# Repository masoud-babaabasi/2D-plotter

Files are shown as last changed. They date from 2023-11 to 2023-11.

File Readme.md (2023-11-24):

# 2D plotter(Using Pen)
### My bachelor's degree final project
This project is inspired by a device called [AxiDraw](https://www.axidraw.com/). This device holds a pen and then draws like anything that is programmed on it, like a human being. I decided to replicate this device functionality and build a device for myself and decided to present it as my bachelor's degree project.

## Mechanical Structure
This project relies on a mechanical structure called T-bot.

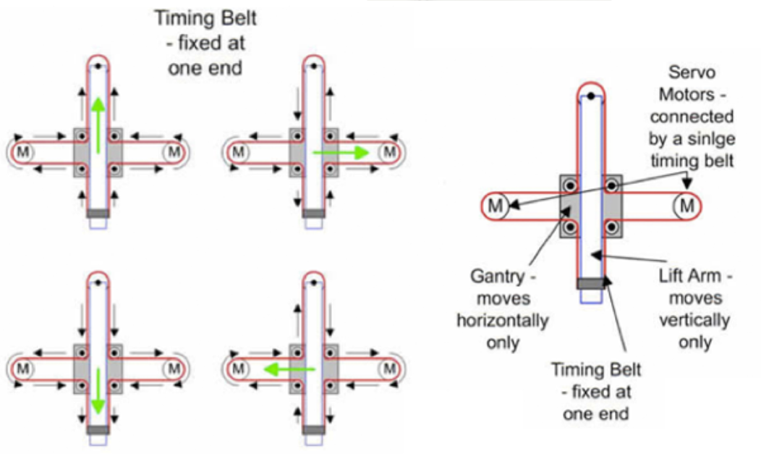
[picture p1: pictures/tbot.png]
t-bot structure

I made the mechanical structure using some CNC machine parts like timing belt, pulleys, rails, and wagons. The advantages of using a T-bot structure is that the motors are fixed and mounted on the chasie and it only needs one timing belt. In this picture two stepper motors are mounted on the sides of one of the rails. The second rail is moving alongside the first one.

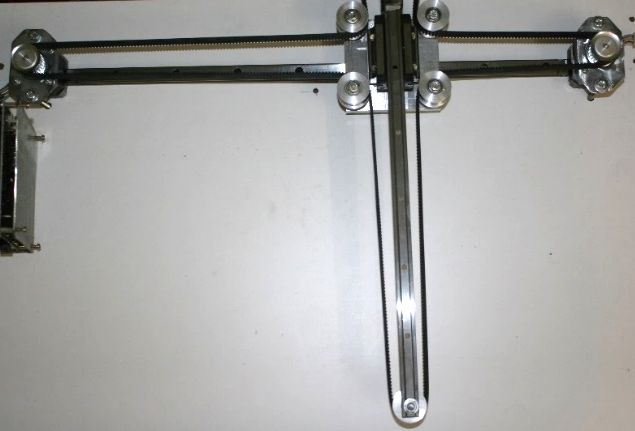
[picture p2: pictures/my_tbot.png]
my t-bot

## Electronic Hardware
I designed the board for the project using Altium Designer. The board is powered by an Atmega2560. There are two L298 power amplifiers for driving each stepper motor. A 2 by 16 character LCD displays the messages and a 4 by 4 keypad alongside a joystick are utilized to receive input from the user. A little servo motor is mounted on the pen holder which can lift the pen up whenever needed. The board supply is 12 volts and there are 3 switching LM2596 that provide adequate voltages for motors and electronics circuit.
board
## Software
The code for the project is written in [Arduino](https://www.arduino.cc/). I also wrote a custom library for controlling the T-bot structure in C++.
For testing there I draw some geometric shapes like spirals. These spirals are drawn via calculation of some polar equations. 
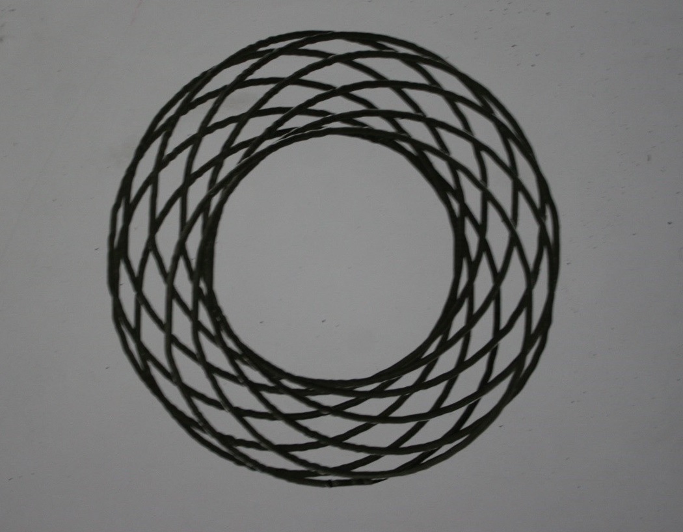
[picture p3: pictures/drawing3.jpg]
spiral

For drawing random shapes like humans, first, we need to draw or insert the shape in one of the CNC machine software. The software then outputs in a format called G-code. Conventional CNC machines can interpret this G-code and do the moves. But my Arduino code can not read G-code and only accepts inputs in the form of XY coordinates. So I wrote a Matlab script that reads the G-code file and outputs the XY sequence. 

In the pictures below, you can see my name being written. The drawing is converted from a G-code that I extracted.
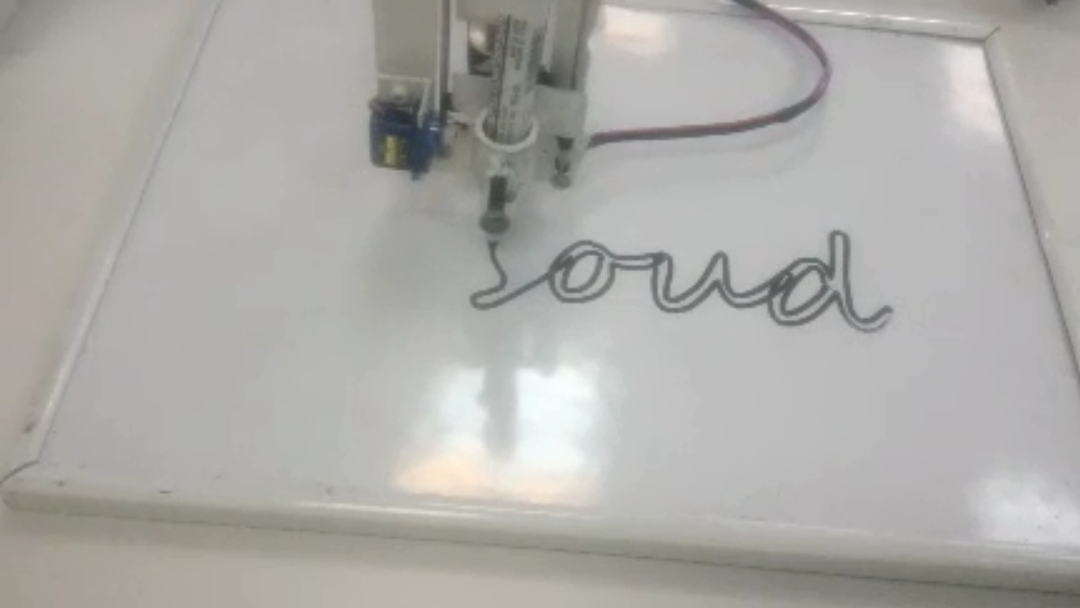
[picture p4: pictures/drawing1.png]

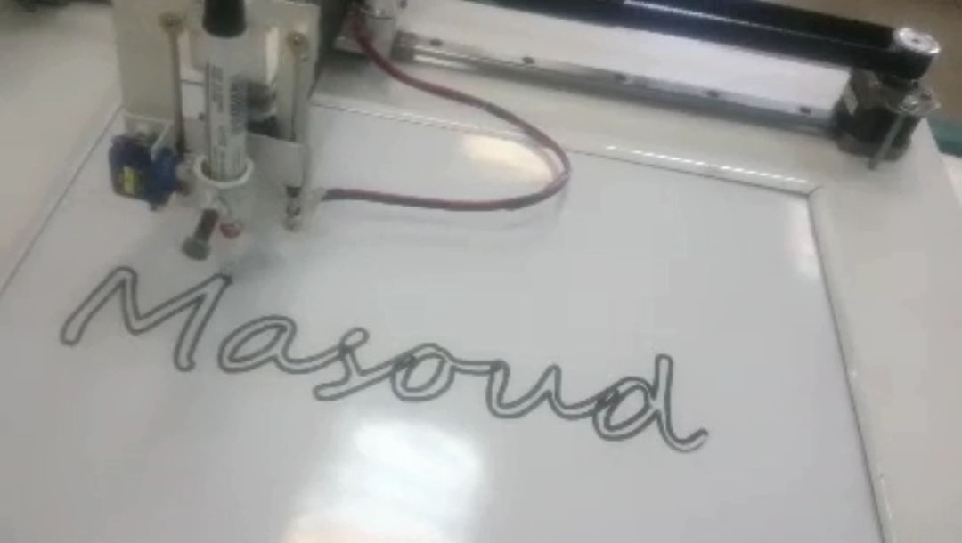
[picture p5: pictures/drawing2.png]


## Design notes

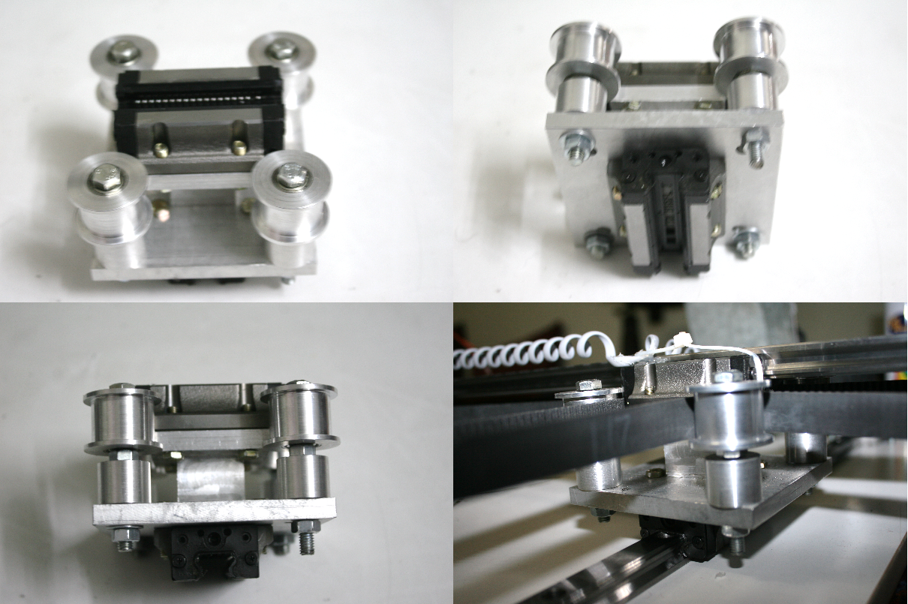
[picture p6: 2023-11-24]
pictures/wagon.png

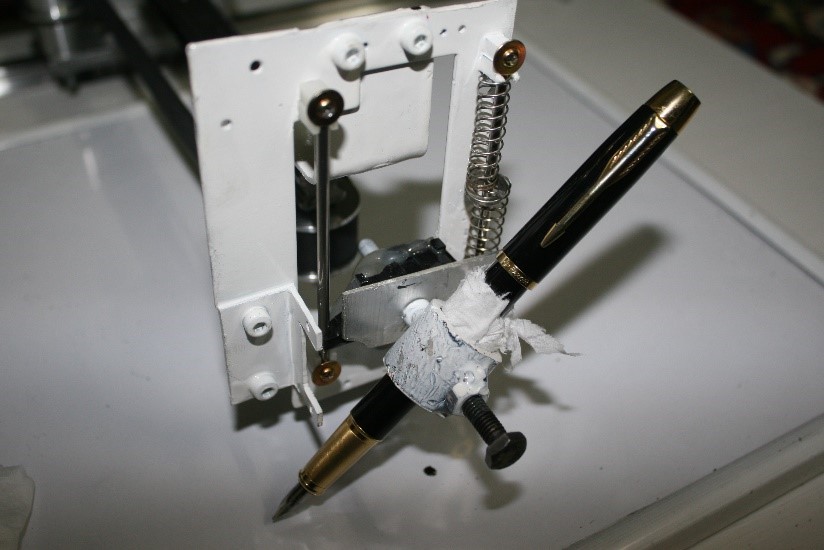
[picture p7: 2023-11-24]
pictures/pen_holder.jpg

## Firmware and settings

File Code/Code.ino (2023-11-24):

#include <Servo.h>
#include <Keypad.h>
#include <LiquidCrystal.h>
#include <Stepper.h>
#include <SPI.h>
#include <SD.h>
/* 
 *  Author: Masoud Babaabasi 
 *  Email: masoud.tafresh@gmail.com
 *  Version 1 created 28/8/2017
 *  For the perpose of this project the origanal library of Arduino PINS "pins_arduino.h" 
 *  for mega2560 is changed 
 *  "C:\Program Files\arduino-1.8.3\hardware\arduino\avr\variants\mega\pins_arduino.h"
 *  The changes are{
 *                            changing PG5 to PH2 for digital pin NO4 //lines 169 and 244
 *                            changing PG2 to PE6 for digital pin NO 39 // line 204 and 279
 *                            changing PG1 to PE2 for digital pin NO 40//line 205 and 
 *                            }
  */
/************************************************************************************************************************************/
/************************************************************************************************************************************/
/*
 * pin assignment
 */
#define SERVO_PIN 11
#define LCD_BACK A14
#define BUZ A15

#define Y_AX A0
#define X_AX A1
#define JOY_SW A3

#define ST1_1 43
#define ST1_2 42
#define ST1_3 45
#define ST1_4 44
#define ST1_E 46

#define ST2_1 3
#define ST2_2 39
#define ST2_3 5
#define ST2_4 2
#define ST2_E 40
#define stepsPerRevolution 200

#define MS1 25  // Micro switch NO1
#define MS2 26  // Micro switch NO2
#define MS3 27  // Micro switch NO3
#define MS4 28  // Micro switch NO4

#define chipSelect 10 // chip select of SD card

#define Rd 13  //reduis of the pully
#define UP 180
#define DOWN 90

#define LCD_ON digitalWrite(LCD_BACK,HIGH)
#define LCD_OFF digitalWrite(LCD_BACK,LOW)
#define BUZ_ON digitalWrite(BUZ,HIGH)
#define BUZ_OFF digitalWrite(BUZ,LOW)
#define ST1_EN digitalWrite(ST1_E,HIGH)
#define ST2_EN digitalWrite(ST2_E,HIGH)
#define ST1_DIS digitalWrite(ST1_E,LOW)
#define ST2_DIS digitalWrite(ST2_E,LOW)
#define HomeX -200
#define HomeY -130
#define xMax 200
#define xMin -200
#define yMax 130
#define yMin -130
/************************************************************************************************************************************/
/************************************************************************************************************************************/
LiquidCrystal lcd(A8, A9, A10, A11, A12, A13);
/************************************************************************************************************************************/
/************************************************************************************************************************************/
const byte ROWS = 3; //three rows
const byte COLS = 3; //three columns
char keys[ROWS][COLS] = {
  {'1','2','3'},
  {'4','5','6'},
  {'7','8','9'},
};
byte rowPins[ROWS] = {7,8,9}; //connect to the row pinouts of the keypad
byte colPins[COLS] = {4, 6,53}; //connect to the column pinouts of the keypad

Keypad keypad = Keypad( makeKeymap(keys), rowPins, colPins, ROWS, COLS );
/************************************************************************************************************************************/
/************************************************************************************************************************************/
Servo pen;
Stepper stepper1(stepsPerRevolution, ST1_1, ST1_2, ST1_3, ST1_4);
Stepper stepper2(stepsPerRevolution, ST2_1, ST2_2, ST2_3, ST2_4);
/************************************************************************************************************************************/
/************************************************************************************************************************************/
float preX,preY,preZ;
int sp = 120;
File shape,back;
/************************************************************************************************************************************/
/************************************************************************************************************************************/
void gotoXY(float inX,float inY);
void goHome();
void drawSnail(float centerX, float centerY);
void drawRose(float centerX, float centerY, float R);
void manualDraw();
void drawStar(float centerX, float centerY, float R);
void drawFiveangle(float centerX, float centerY, float A);
void drawStar2(float centerX, float centerY, float R);
void drawCircle(float centerX, float centerY, float R);
void spirograph(float r,float R,float w,bool sign);
void spirograph2();
/************************************************************************************************************************************/
/************************************************************************************************************************************/
void setup() {
 pen.attach(SERVO_PIN); 
 pen.write(UP);
 Serial.begin(115200);
 lcd.begin(16, 2);
pinMode(LCD_BACK,OUTPUT);
pinMode(BUZ,OUTPUT);
pinMode(ST2_E,OUTPUT);
pinMode(ST2_E,OUTPUT);
ST1_EN;
ST2_EN;
preX = HomeX;
preY = HomeY;
preZ = 1;
lcd.print("setup OK!");
LCD_ON;
delay(600);
lcd.clear();
/**********************************/
/**********************************/
stepper1.setSpeed(sp);
stepper2.setSpeed(sp);
//drawSnail(0,0);
//drawRose(0,0,80);
//drawStar(0,0,80);
//drawFiveangle(0,0,94);
//drawStar2(0,0,80);
//spirograph(70,20,10,0);
//spirograph2();
//drawCircle(0,0,100);
/*for(int i=5;i<=80;i+=15) {
  drawCircle(0,0,i);
  delay(600);
}*/
/*for(int i=5;i<=85;i+=10) {
  drawRose(0,0,i);
  delay(600);
}*/
  //draw Square
  /*gotoXY(80,80);
  gotoXY(80,-80);
  gotoXY(-80,-80);
  gotoXY(-80,80);
  gotoXY(80,80);*/
  //SD card read formated data
   /*if (!SD.begin(chipSelect)) lcd.print(F("Card failed, or not present"));
   shape = SD.open("masoud.txt", FILE_READ);
   back = SD.open("backup.txt",FILE_WRITE);
   shape.setTimeout(1);
   if(shape){
    String str,stX,stY;
    float x,y;
    while(shape.position() != shape.size()){
    str =shape.readStringUntil(',');
    if( str.startsWith(F("x=-")))  {
      stX = str.substring(3);
      x = stX.toFloat();
      x= -x;
    }
   else if( str.startsWith(F("x=")))  {
      stX = str.substring(2);
      x = stX.toFloat();
    }
      str =shape.readStringUntil('\n');
    if( str.startsWith(F("y=-")))  {
      stY = str.substring(3);
      y = stY.toFloat();
      y= -y;
    }
   else if( str.startsWith(F("y=")))  {
      stY = str.substring(2);
      y = stY.toFloat();
    }
    gotoXY(x,y);
    //back.print("x=");
    //back.print(x);
    //back.print(",y=");
   // back.println(y);
   // for(int i=0;i<5;i++) str =shape.readStringUntil('\n');
    }

   }
   shape.close();
   back.close();
   lcd.print("done");*/
   
}
void loop() {
  int i;
  String rec,stX,stY,stZ,str;
  float x,y,z;
 char key = keypad.getKey();
 if(key){
  lcd.clear();
  lcd.print(key);
  switch(key){
    case '1': lcd.print("Draw a star");
                  drawStar2(0,0,80);
                  lcd.clear();
                  break;
   case '2': lcd.print("Draw a pentagonangle");
                  drawFiveangle(0,0,94);
                  lcd.clear();
                  break;
   case '3': lcd.print("Draw a Rose");
                  drawRose(0,0,80);
                  lcd.clear();
                  break;
   case '4': lcd.print("Draw a Spirograph");
                  spirograph(70,20,10,0);
                  lcd.clear();
                  break;
   case '5': lcd.print("Draw a Spirograph");
                  spirograph2();
                  lcd.clear();
                  break;
   case '6': lcd.print("Draw a Snail");
                  drawSnail(0,0);
                  lcd.clear();
                  break;
   case '7': lcd.print("Draw masoud");
                    if (!SD.begin(chipSelect)) lcd.print(F("Card failed, or not present"));
                       shape = SD.open("part.txt", FILE_READ);
                       shape.setTimeout(1);
                       if(shape){

                        while(shape.position() != shape.size()){
                        str =shape.readStringUntil(',');
                        if( str.startsWith(F("x=-")))  {
                          stX = str.substring(3);
                          x = stX.toFloat();
                          x= -x;
                        }
                       else if( str.startsWith(F("x=")))  {
                          stX = str.substring(2);
                          x = stX.toFloat();
                        }
                          str =shape.readStringUntil(',');
                        if( str.startsWith(F("y=-")))  {
                          stY = str.substring(3);
                          y = stY.toFloat();
                          y= -y;
                        }
                       else if( str.startsWith(F("y=")))  {
                          stY = str.substring(2);
                          y = stY.toFloat();
                        }
                        str =shape.readStringUntil('\n');
                        if( str.startsWith(F("z=-")))  {
                          stZ = str.substring(3);
                          z = stZ.toFloat();
                          z= -z;
                        }
                       else if( str.startsWith(F("z=")))  {
                          stZ = str.substring(2);
                          z = stZ.toFloat();
                        }
                        if(z>0 && preZ<0) {
                          pen.write(UP);
                          delay(500);
                        }
                        else if(z<0 && preZ>0) {
                          pen.write(DOWN);
                          delay(500);
                        }
                        gotoXY(x,y);
                        preZ = z;
                       // for(int j=0;j<30;j++) str =shape.readStringUntil('\n');
                        }
                       }
                       shape.close();
                       lcd.print("done");
                       goHome();
                  break;
  
  }
 }
 if(Serial.available()){
  rec =Serial.readStringUntil(',');
    if( rec.startsWith(F("x=")))  {
      stX = rec.substring(2);
      x = stX.toFloat();
    }
      rec =Serial.readStringUntil('\n');
    if( rec.startsWith(F("y=")))  {
      stY = rec.substring(2);
      y = stY.toFloat();
    }
    gotoXY(x,y);
    
 }

}
/************************************************************************************************************************************/
/************************************************************************************************************************************/
void gotoXY(float inX,float inY){
    int N1,N2,n1,n2;
    int Np1,Np2;
  float coef;
    float dx,dy,X,Y;
  uint32_t t,lastT;
  uint32_t interval1,interval2;
  Np1 = Np2 = 0;
  if(inX > xMax) X = xMax;
  else if(inX < xMin) X = xMin;
  else X = inX;
    if(inY > yMax) Y = yMax;
  else if(inY < yMin) Y = yMin;
  else Y = inY;
  dx = X - preX;
  dy = Y - preY;

  coef =  200 / ( 2.0  * PI * Rd);//coef = SperR / ( 2.0  * PI * reduis);
 
  N1 = ( coef * dx ) + ( coef * dy);
  N2 = ( coef * dx ) + ( -coef * dy);

  n1 = abs(N1);
  n2= abs(N2);
  if( n1 == n2 ){
    stepper1.setSpeed(sp/sqrt(2));
    stepper2.setSpeed(sp/sqrt(2));
    for(int i = 0;i<n1;i++){
    stepper1.step(N1/n1);
    stepper2.step(N2/n2);
    }
  }
  else{
    stepper1.setSpeed(sp);
    stepper2.setSpeed(sp);
  t = (max(n1,n2) * 60.0) / ( 120 * 200 )  * 1000000.0; // time in microsec

  if( N1 == 0 ) interval1 = 0;
  else interval1 = t / abs(N1);
  if( N2 == 0 ) interval2 = 0;
  else interval2 = t / abs(N2);

  lastT = micros();

  while(1){
      if( micros() - lastT > ( (Np1+1) * interval1 ) ) 
      {
        if(N1 && Np1 < abs(N1)){
                    stepper1.step(N1/n1);
                    Np1++; 

        }
      }
      if( micros() - lastT > ( (Np2+1) * interval2 ) ) 
      {
        if(N2 && Np2 < abs(N2)){
                    stepper2.step(N2/n2);
                    Np2++; 
        }
      }
      if( Np1 == abs(N1) && Np2 == abs(N2) ) break;
  }
  }
  dx =  (1 / (2 * coef)) * ( N1 + N2);
  dy =  (1 / (2 * coef)) * ( N1 - N2); 
  preX += dx;
  preY += dy;

  Serial.println("ready");
}
/************************************************************************************************************************************/
/************************************************************************************************************************************/
void goHome(){
  pen.write(UP);
  gotoXY(HomeX,HomeY);
}
/************************************************************************************************************************************/
/************************************************************************************************************************************/
void drawSnail(float centerX, float centerY){
  float x,y,theta,r;
  gotoXY(centerX,centerY);
  pen.write(DOWN);
  for( theta = 0 ; theta <= ( 8 * PI ) ; theta+=0.001){
    r = 20 / ( 2 * PI ) * theta;
    x = centerX + r * cos(theta);
    y = centerY + r * sin(theta);
    gotoXY(x,y);
  }
  goHome();
}
/************************************************************************************************************************************/
/************************************************************************************************************************************/
void drawRose(float centerX, float centerY, float R){
  float x,y,theta,r;
  gotoXY(centerX,centerY);
  for( theta = 0 ; theta <= ( 2 * PI ) ; theta+=0.008){
    r = R * sin(3*theta);
    x = centerX + r * cos(theta);
    y = centerY + r * sin(theta);
    gotoXY(x,y);
  }
  goHome();
}
/************************************************************************************************************************************/
/************************************************************************************************************************************/
void manualDraw(){
int val1,val2;
int DELAY = 180;
int SPEED = 180;
val1 = analogRead(Y_AX); 
val2 = analogRead(X_AX); 
if( val1<520 && val1 > 500 ) val1 = 512;
if( val2<520 && val2 > 500 ) val2 = 512;
int MAX = (2 * PI *  Rd * SPEED * DELAY)/60000; //rd = 13  , speed = 150 , delay = 100ms
val1 = map(val1, 0, 1023, MAX, -MAX);  //formula for maping between timiming intervals {max = (2*pi*Rd*speed*interval)/ 60000}
val2 = map(val2, 0, 1023, -MAX, MAX);  
Serial.print("val1 = ");
Serial.println(val1);
Serial.print("val2 = ");
Serial.println(val2);
val1 += preX;
val2 += preY;
if(digitalRead(JOY_SW)) pen.write(UP);
else pen.write(DOWN);
gotoXY(val1,val2);
lcd.clear();
lcd.print("X = ");
lcd.print(val1);
lcd.print(",Y = ");
lcd.print(val2);
}
/************************************************************************************************************************************/
/************************************************************************************************************************************/
void drawStar(float centerX, float centerY, float R){
  float x,y;
  gotoXY(centerX,centerY+R);
  pen.write(DOWN);
  gotoXY(centerX+( R * sin(PI * 36 /180)),centerY-( R * cos(PI * 36 /180)));
  gotoXY(centerX- ( R * cos(PI * 18 /180)),centerY+( R * sin(PI * 18 /180)));
  gotoXY(centerX+( R * cos(PI * 18 /180)),centerY+(R * sin(PI * 18 /180)));
  gotoXY(centerX-( R * sin(PI * 36 /180)),centerY-( R * cos(PI * 36 /180)));
  gotoXY(centerX,centerY+R);
  goHome();
}
/************************************************************************************************************************************/
/************************************************************************************************************************************/
void drawFiveangle(float centerX, float centerY, float A){
  float x,y;
  float R = A / ( 2 * sin( PI * 36 / 180));
  gotoXY(centerX,centerY+R);
  pen.write(DOWN);
  delay(300);
  gotoXY(centerX+( R * cos(PI * 18 /180)),centerY+(R * sin(PI * 18 /180)));
  delay(300);
  gotoXY(centerX+( R * sin(PI * 36 /180)),centerY-( R * cos(PI * 36 /180)));
  delay(300);
  gotoXY(centerX-( R * sin(PI * 36 /180)),centerY-( R * cos(PI * 36 /180)));
  delay(300);
  gotoXY(centerX- ( R * cos(PI * 18 /180)),centerY+( R * sin(PI * 18 /180)));
  delay(300);
  gotoXY(centerX,centerY+R);
  pen.write(UP);
  goHome();
}
/************************************************************************************************************************************/
/************************************************************************************************************************************/
void drawStar2(float centerX, float centerY, float R){
  float x,y;
  float r = R * sin(PI * 18 / 180) / cos(PI * 36 /180);
  
  gotoXY(centerX,centerY+R);
  pen.write(DOWN);
  delay(1000);
  gotoXY(centerX+( r * sin(PI * 36 /180)),centerY+( R * sin(PI * 18 /180)));
  delay(1000);
  gotoXY(centerX+( R * cos(PI * 18 /180)),centerY+( R * sin(PI * 18 /180)));
  delay(1000);
  gotoXY(centerX+ ( r * cos(PI * 18 /180)),centerY-( r * sin(PI * 18 /180)));
  delay(1000);
  gotoXY(centerX+( R * sin(PI * 36 /180)),centerY-(R * cos(PI * 36 /180)));
  delay(1000);
  gotoXY(centerX,centerY- r );
  delay(1000);
  gotoXY(centerX-( R * sin(PI * 36 /180)),centerY-(R * cos(PI * 36 /180)));
  delay(1000);
  gotoXY(centerX- ( r * cos(PI * 18 /180)),centerY-( r * sin(PI * 18 /180)));
  delay(1000);
  gotoXY(centerX-( R * cos(PI * 18 /180)),centerY+( R * sin(PI * 18 /180)));
  delay(1000);
  gotoXY(centerX-( r * sin(PI * 36 /180)),centerY+( R * sin(PI * 18 /180)));
  delay(1000);
  gotoXY(centerX,centerY+R);
  goHome();

}
/************************************************************************************************************************************/
/************************************************************************************************************************************/
void drawCircle(float centerX, float centerY, float R){
  float x,y,theta;
  gotoXY(centerX+R,centerY);
  pen.write(DOWN);
  for( theta = 0 ; theta <= ( 2 * PI ) ; theta+=.001){
    x = centerX + R * cos(theta);
    y = centerY + R * sin(theta);
    gotoXY(x,y);
  }
  goHome();
}
/************************************************************************************************************************************/
/************************************************************************************************************************************/
void spirograph(float r,float R,float w,bool sign){
float x,y;
float theta;
gotoXY(0,R+r);
pen.write(DOWN);
if(sign){
  for( theta = 0 ; theta <= ( 2 * PI ) ; theta+=1){
    x = R * sin(theta) + r * sin( w * theta);
    y = R * cos(theta) + r * cos( w * theta);
    gotoXY(x,y);
  }
}
else {
    for( theta = 0 ; theta <= ( 2 * PI ) ; theta+=1){
    x = R * sin(theta) - r * sin( w * theta);
    y = R * cos(theta) + r * cos( w * theta);
    gotoXY(x,y);
  }
}
goHome();
}
/************************************************************************************************************************************/
/************************************************************************************************************************************/
void spirograph2(){
float x,y;
float theta;
float r,R1,R2,w;
r=150;
R1=20;
w = 0.5;
R2 = 50;
gotoXY( 0 , 0.5 * ( R2 + 0.6 * (R1 + r)) );
pen.write(DOWN);
  for( theta = 0 ; theta <= ( 200 * PI ) ; theta+=0.05){
    x = 0.5 * ( R2 * sin(0.01 * theta) + 0.6 * ( R1 * sin(theta) - r * sin( w * theta)) );
    y = 0.5 * ( R2 * cos(0.01 * theta) + 0.6 * (R1 * cos(theta) + r * cos( w * theta)) );
    gotoXY(x,y);
  }
  goHome();
}

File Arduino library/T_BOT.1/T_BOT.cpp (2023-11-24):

#include "T_BOT.h"
#include "arduino.h"
T_BOT::T_BOT(int SR, int R, int Sp, int st11, int st12, int st13, int st14, int st1E,
                                    int st21, int st22, int st23, int st24, int st2E, 
                                    int servoPin):
                                    stp1(SperR, st11, st12, st13, st14),
                                    stp2(SperR, st21, st22, st23, st24){
  SperR = SR;
  reduis = R;
  stpSpeed = Sp;
  st1e = st1E;
  st2e = st2E;
  pen.attach(servoPin);
  pinMode(st1e,OUTPUT);
  pinMode(st2e,OUTPUT);
  digitalWrite(st1e,HIGH);
  digitalWrite(st2e,HIGH);
  stp1.setSpeed(stpSpeed);
  stp2.setSpeed(stpSpeed);
  coef = SperR / ( 2.0  * PI * reduis);
  preX = preY = 0;
}

void T_BOT::gotoxy(float X,float Y){
  int Np1,Np2;
  float dx,dy;
  uint32_t t,lastT;
  uint32_t interval1,interval2;
  Np1 = Np2 = 0;
  dx = X - preX;
  dy = Y - preY;
  
  N1 = ( -coef * dx ) + (-coef * dy);
  N2 = ( coef * dx ) + ( -coef * dy);
  
  t = ((max(abs(N1),abs(N2))) * 60.0) / ( stpSpeed * SperR )  * 1000000.0; // time in microsec

  if( N1 == 0 ) interval1 = t;
  else interval1 = t / abs(N1);
  if( N2 == 0 ) interval2 = t;
  else interval2 = t / abs(N2);
  
  digitalWrite(st1e,HIGH);
  digitalWrite(st2e,HIGH);
  
  lastT = micros();
  while(1){
      if( micros() - lastT > ( (Np1+1) * interval1 ) ) 
      {
        if(N1){
                    if(Np1 < abs(N1)){
                    if(N1 > 0) stp1.step(1);
                    else stp1.step(-1);
                    Np1++; 
                    }
        }
      }
      if( micros() - lastT > ( (Np2+1) * interval2 ) ) 
      {
        if(N2){
                    if(Np2 < abs(N2)){
                    if(N2 > 0) stp2.step(1);
                    else stp2.step(-1);
                    Np2++; 
                    }
        }
      }
      if( Np1 == abs(N1) && Np2 == abs(N2) ) break;
  }
  digitalWrite(st1e,LOW);
  digitalWrite(st2e,LOW);
  preX = X;
  preY = Y;
}

void T_BOT::upDown(bool UP_DOWN){
	if(UP_DOWN) pen.write(up);
	else pen.write(down);
}
float T_BOT::getX(){
	return preX;
}
float T_BOT::getY(){
	return preY;
}
